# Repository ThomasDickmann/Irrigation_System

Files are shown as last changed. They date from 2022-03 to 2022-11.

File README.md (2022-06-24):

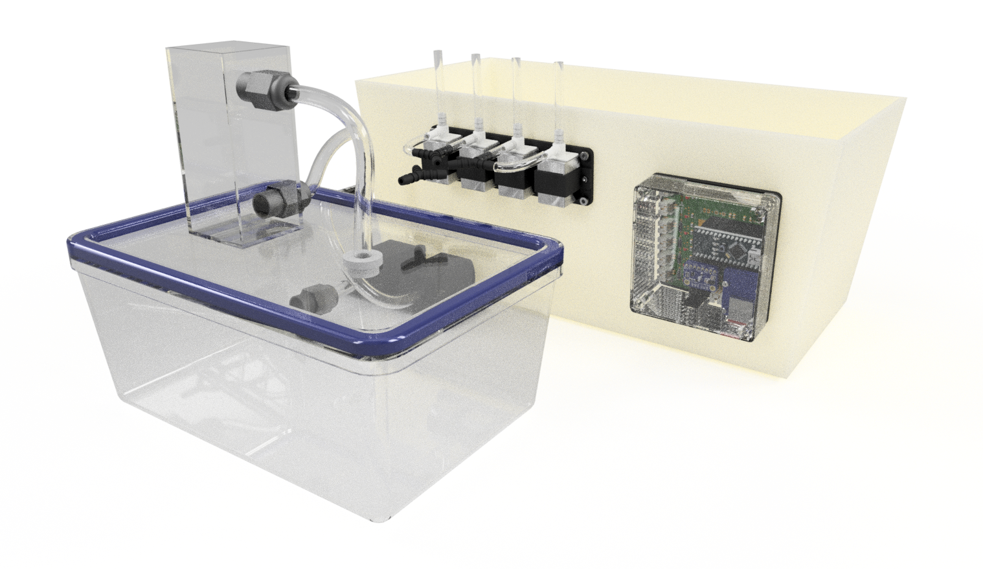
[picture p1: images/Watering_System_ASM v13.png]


# Arduino Irrigation System - WIP
The purpose of this project was to learn basic electronic design, PCB layout, and embedded software development using VS code and PlatformIO.
The project is a work in progress, so use any code with appropriate caution!

Written in 2022 by Thomas Dickmann. 

## System architecture and intended use 
The goal is to create a fully automated irrigation system to be used in a home automation context. The hardware is capable of controlling two 12V pumps and four 12V solenoid valves to independently give water to up to four plants. The dual pump setup is used to create a redundant safety feature to prevent flooding upon a controller malfunction. The soil moisture level is obtained using capacitive analog sensors. Additionally, a BMP280 temperature and pressure sensor can provide ambient information. Finally, the connection of a SD card module allows for data logging and a Real Time Clock (RTC) provides time stamps and allows the system to operate in an energy efficient deep sleep state in between the service routines.     

## Content 
This repo currently contains the arduino code for the controller. The project also comprises Autodesk EAGLE files for the schematic and PCB as well as a CAD package with Fusion360 and .stl files for the various mechanical parts to put together the final product. Additionally, off-the-shelf components make up a substantial part of the system, therefore a list will be published containing links to the various components that were used. 
Finally, a manual will be created after everything is wrapped up and tested. 

### Features
+ 6 MOSFET Low side switches (LSS) with indicator LEDs for valves and motors, providing 12V input power to the peripherals 
+ PWM enabled motor control for power modulation 
+ 4 analog sensor inputs with filter capacitors 
+ High Side Switch (HSS) controlling the powering of the analog sensors and SD card (powered only when in use to reduce idle energy consumption) 
+ Data logging of soil moisture levels, temperature and air pressure with time stamps for long term observation  

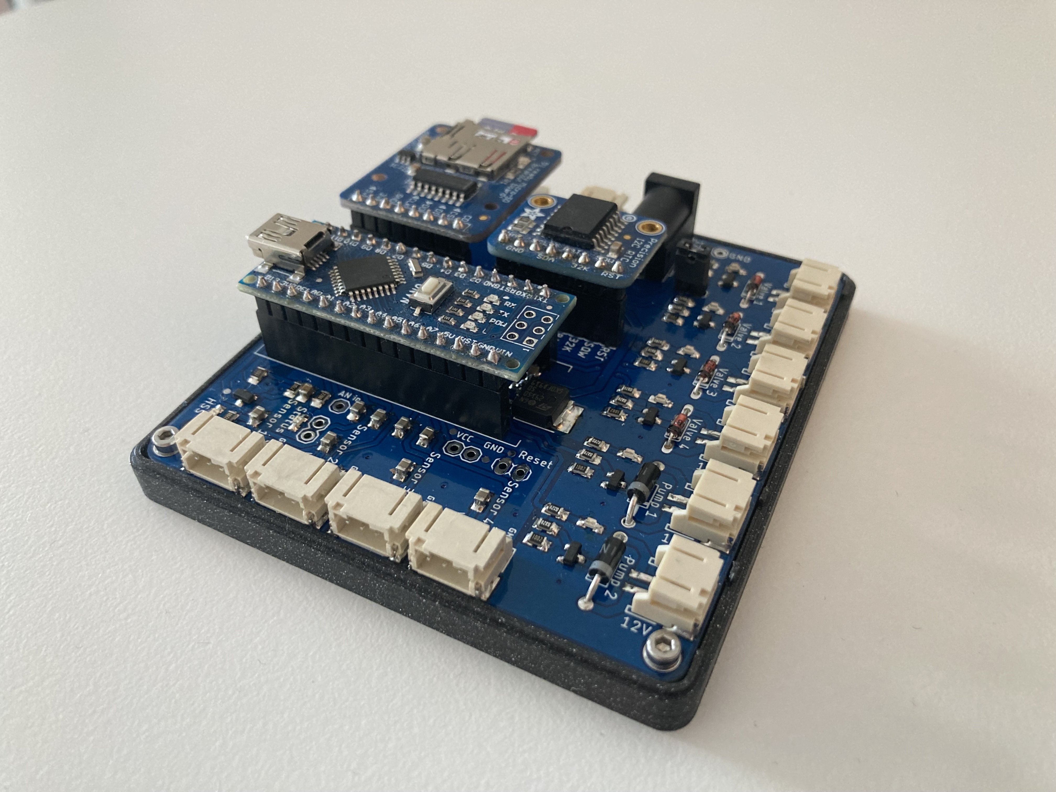
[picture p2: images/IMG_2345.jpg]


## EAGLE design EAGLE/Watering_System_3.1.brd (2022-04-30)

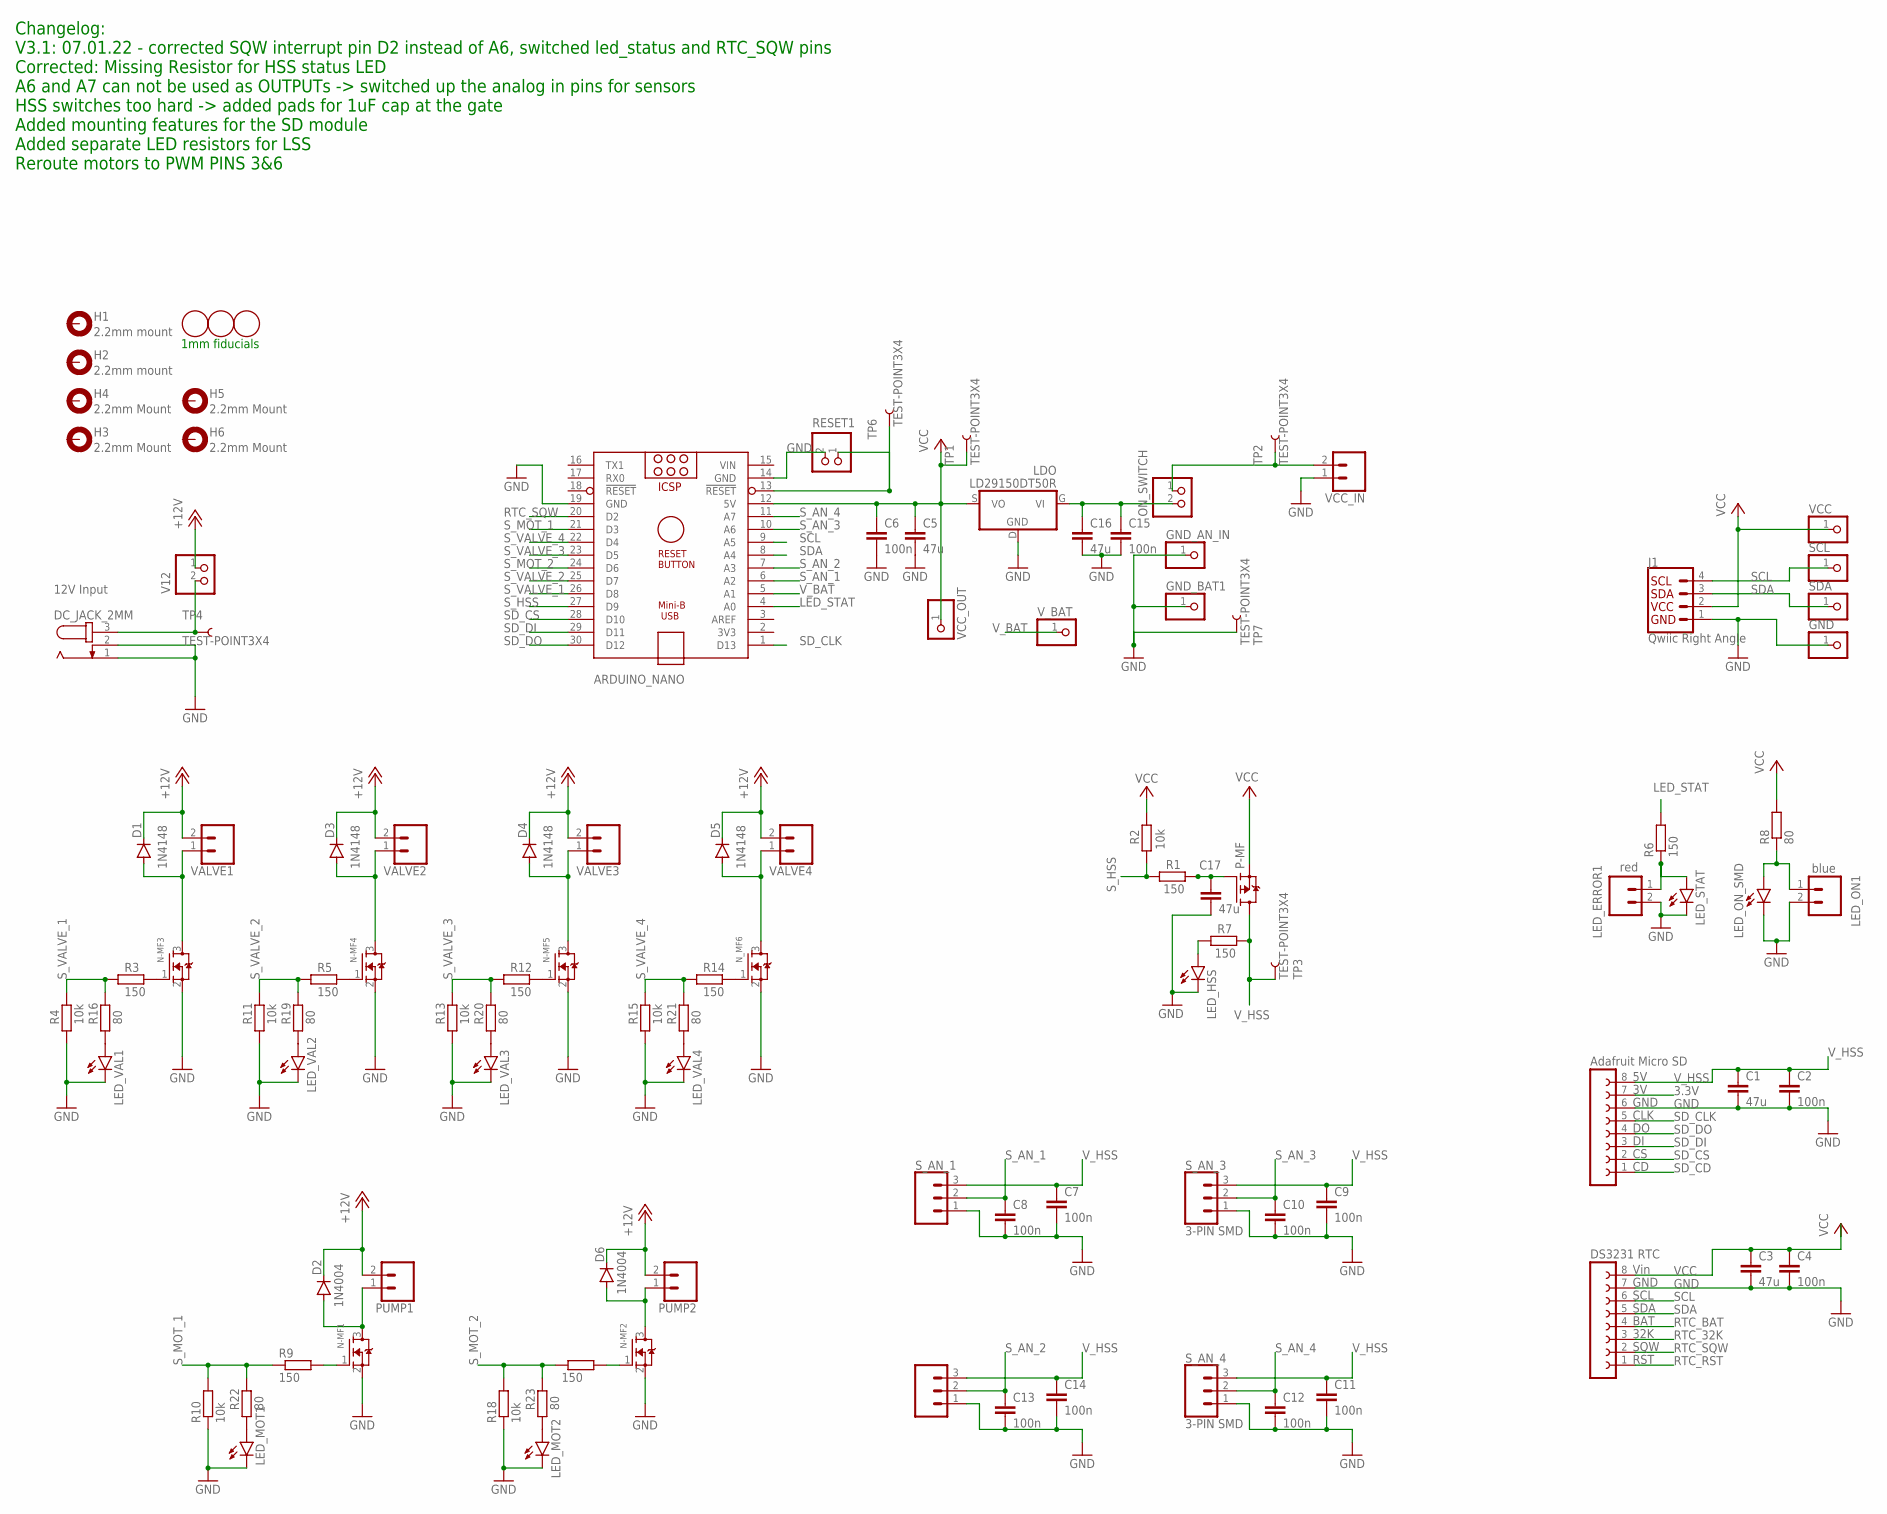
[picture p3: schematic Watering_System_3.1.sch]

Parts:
ARDUINO_NANO: ARDUINO_NANO
C1, C3, C5, C16, C17: 47u; C0805
C2, C4, C6, C7, C8, C9, C10, C11, C12, C13, C14, C15: 100n; C0805
D1, D3, D4, D5: 1N4148; DO35-7
D2, D6: 1N4004; DO41-10
DC_JACK_2MM: 12V Input; SPC4077
GND: PINHD-1X1; 1X01
GND_AN_IN: PINHD-1X1; 1X01
GND_BAT1: PINHD-1X1; 1X01
H1, H2: 2.2mm mount; 2,2-PAD
H3, H4, H5, H6: 2.2mm Mount; 2,2-PAD
J1: Qwiic Right Angle; 1X04_1MM_RA
LDO: LD29150DT50R; DPACK_2
LED_ERROR1: red; 1X02
LED_HSS: LEDCHIPLED_0805; CHIPLED_0805
LED_MOT1, LED_MOT2: LEDCHIPLED_0805; CHIPLED_0805
LED_ON1: blue; 1X02
LED_ON_SMD: LEDCHIPLED_0805; CHIPLED_0805
LED_STAT: LEDCHIPLED_0805; CHIPLED_0805
LED_VAL1, LED_VAL2, LED_VAL3, LED_VAL4: LEDCHIPLED_0805; CHIPLED_0805
N-MF1, N-MF2, N-MF3, N-MF4, N-MF5: IRLML6244TRPBF; SOT23R_INFINEON
N_MF6: IRLML6244TRPBF; SOT23R_INFINEON
ON_SWITCH: toggle_breakout; 1X02
P-MF: IRLML2244TRPBF; SOT23R_INFINEON
PUMP1, PUMP2: CONN_02-JST-2MM-SMT; JST-2-SMD
R1, R3, R5, R6, R7, R9, R12, R14, R17: 150; R0805
R2, R4, R10, R11, R13, R15, R18: 10k; R0805
R8, R16, R19, R20, R21, R22, R23: 80; R0805
RESET1: toggle_breakout; 1X02
RTC: DS3231; RTC
SCL: PINHD-1X1; 1X01
SC_CARD: MIRCO_SD_ADAFRUITSD; ADAFRUIT_SD
SDA: PINHD-1X1; 1X01
S_AN_1, S_AN_2, S_AN_3, S_AN_4: 3-PIN SMD; JST-3-SMD
TP1, TP2, TP3, TP4, TP6, TP7: TEST-POINT3X4; PAD.03X.04
U$1, U$2, U$3: FIDUCIAL; FIDUCIAL_1MM
V12: toggle_breakout; 1X02
VALVE1, VALVE2, VALVE3, VALVE4: CONN_02-JST-2MM-SMT; JST-2-SMD
VCC: PINHD-1X1; 1X01
VCC_IN: CONN_02-JST-2MM-SMT; JST-2-SMD
VCC_OUT: PINHD-1X1; 1X01
V_BAT: PINHD-1X1; 1X01

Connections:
3.3V: SC_CARD.7 (3V)
+12V: D1.C, D2.C, D3.C, D4.C, D5.C, D6.C, PUMP1.2 (1), PUMP2.2 (1), V12.1, VALVE1.2 (1), VALVE2.2 (1), VALVE3.2 (1), VALVE4.2 (1)
GND: ARDUINO_NANO.14 (GND), ARDUINO_NANO.19 (GND), C1.2, C2.2, C3.2, C4.2, C5.2, C6.2, C7.2, C8.2, C9.2, C10.2, C11.2, C12.2, C13.2, C14.2, C15.2, C16.2, C17.2, DC_JACK_2MM.1, DC_JACK_2MM.2, GND.1, GND_AN_IN.1, GND_BAT1.1, J1.1, LDO.D (GND), LED_ERROR1.2, LED_HSS.C, LED_MOT1.C, LED_MOT2.C, LED_ON1.2, LED_ON_SMD.C, LED_STAT.C, LED_VAL1.C, LED_VAL2.C, LED_VAL3.C, LED_VAL4.C, N-MF1.2 (S), N-MF2.2 (S), N-MF3.2 (S), N-MF4.2 (S), N-MF5.2 (S), N_MF6.2 (S), R4.1, R10.1, R11.1, R13.1, R15.1, R18.1, RESET1.2, RTC.7 (GND), SC_CARD.6 (GND), S_AN_1.1, S_AN_2.1, S_AN_3.1, S_AN_4.1, TP7.P$1, VCC_IN.1 (2)
LED_STAT: ARDUINO_NANO.4 (A0), R6.2
unnamed: N-MF1.1 (G), R9.2
unnamed: D3.A, N-MF4.3 (D), VALVE2.1 (2)
unnamed: LED_ON1.1, LED_ON_SMD.A, R8.1
unnamed: N-MF2.1 (G), R17.2
unnamed: LED_ERROR1.1, LED_STAT.A, R6.1
unnamed: LED_HSS.A, R7.1
unnamed: D1.A, N-MF3.3 (D), VALVE1.1 (2)
unnamed: N-MF4.1 (G), R5.2
unnamed: D4.A, N-MF5.3 (D), VALVE3.1 (2)
unnamed: C17.1, P-MF.1 (G), R1.2
unnamed: N-MF3.1 (G), R3.2
unnamed: N-MF5.1 (G), R12.2
unnamed: D5.A, N_MF6.3 (D), VALVE4.1 (2)
unnamed: N_MF6.1 (G), R14.2
unnamed: C15.1, C16.1, LDO.G (VI), ON_SWITCH.2
unnamed: DC_JACK_2MM.3, TP4.P$1, V12.2
unnamed: LED_VAL1.A, R16.1
unnamed: D2.A, N-MF1.3 (D), PUMP1.1 (2)
unnamed: D6.A, N-MF2.3 (D), PUMP2.1 (2)
unnamed: LED_VAL2.A, R19.1
unnamed: ARDUINO_NANO.13 (!RESET), RESET1.1, TP6.P$1
unnamed: ON_SWITCH.1, TP2.P$1, VCC_IN.2 (1)
unnamed: LED_VAL3.A, R20.1
unnamed: LED_VAL4.A, R21.1
unnamed: LED_MOT1.A, R22.1
unnamed: LED_MOT2.A, R23.1
RTC_32K: RTC.3 (32K)
RTC_BAT: RTC.4 (BAT)
RTC_RST: RTC.1 (RST)
RTC_SQW: ARDUINO_NANO.20 (D2), RTC.2 (SQW)
SCL: ARDUINO_NANO.9 (A5), J1.4, RTC.6 (SCL), SCL.1
SDA: ARDUINO_NANO.8 (A4), J1.3, RTC.5 (SDA), SDA.1
SD_CD: SC_CARD.1 (CD)
SD_CLK: ARDUINO_NANO.1 (D13), SC_CARD.5 (CLK)
SD_CS: ARDUINO_NANO.28 (D10), SC_CARD.2 (CS)
SD_DI: ARDUINO_NANO.29 (D11), SC_CARD.3 (DI)
SD_DO: ARDUINO_NANO.30 (D12), SC_CARD.4 (DO)
S_AN_1: ARDUINO_NANO.6 (A2), C8.1, S_AN_1.2
S_AN_2: ARDUINO_NANO.7 (A3), C13.1, S_AN_2.2
S_AN_3: ARDUINO_NANO.10 (A6), C10.1, S_AN_3.2
S_AN_4: ARDUINO_NANO.11 (A7), C12.1, S_AN_4.2
S_HSS: ARDUINO_NANO.27 (D9), R1.1, R2.1
S_MOT_1: ARDUINO_NANO.21 (D3), R9.1, R10.2, R22.2
S_MOT_2: ARDUINO_NANO.24 (D6), R17.1, R18.2, R23.2
S_VALVE_1: ARDUINO_NANO.26 (D8), R3.1, R4.2, R16.2
S_VALVE_2: ARDUINO_NANO.25 (D7), R5.1, R11.2, R19.2
S_VALVE_3: ARDUINO_NANO.23 (D5), R12.1, R13.2, R20.2
S_VALVE_4: ARDUINO_NANO.22 (D4), R14.1, R15.2, R21.2
VCC: ARDUINO_NANO.12 (5V), C3.1, C4.1, C5.1, C6.1, J1.2, LDO.S (VO), P-MF.2 (S), R2.2, R8.2, RTC.8 (VIN), TP1.P$1, VCC.1, VCC_OUT.1
VIN: ARDUINO_NANO.15 (VIN)
V_BAT: ARDUINO_NANO.5 (A1), V_BAT.1
V_HSS: C1.1, C2.1, C7.1, C9.1, C11.1, C14.1, P-MF.3 (D), R7.2, SC_CARD.8 (5V), S_AN_1.3, S_AN_2.3, S_AN_3.3, S_AN_4.3, TP3.P$1

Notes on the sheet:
1mm fiducials
Changelog: V3.1: 07.01.22 - corrected SQW interrupt pin D2 instead of A6, switched led_status and RTC_SQW pins Corrected: Missing Resistor for HSS status LED A6 and A7 can not be used as OUTPUTs -> switched up the analog in pins for sensors HSS switches too hard -> added pads for 1uF cap at the gat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

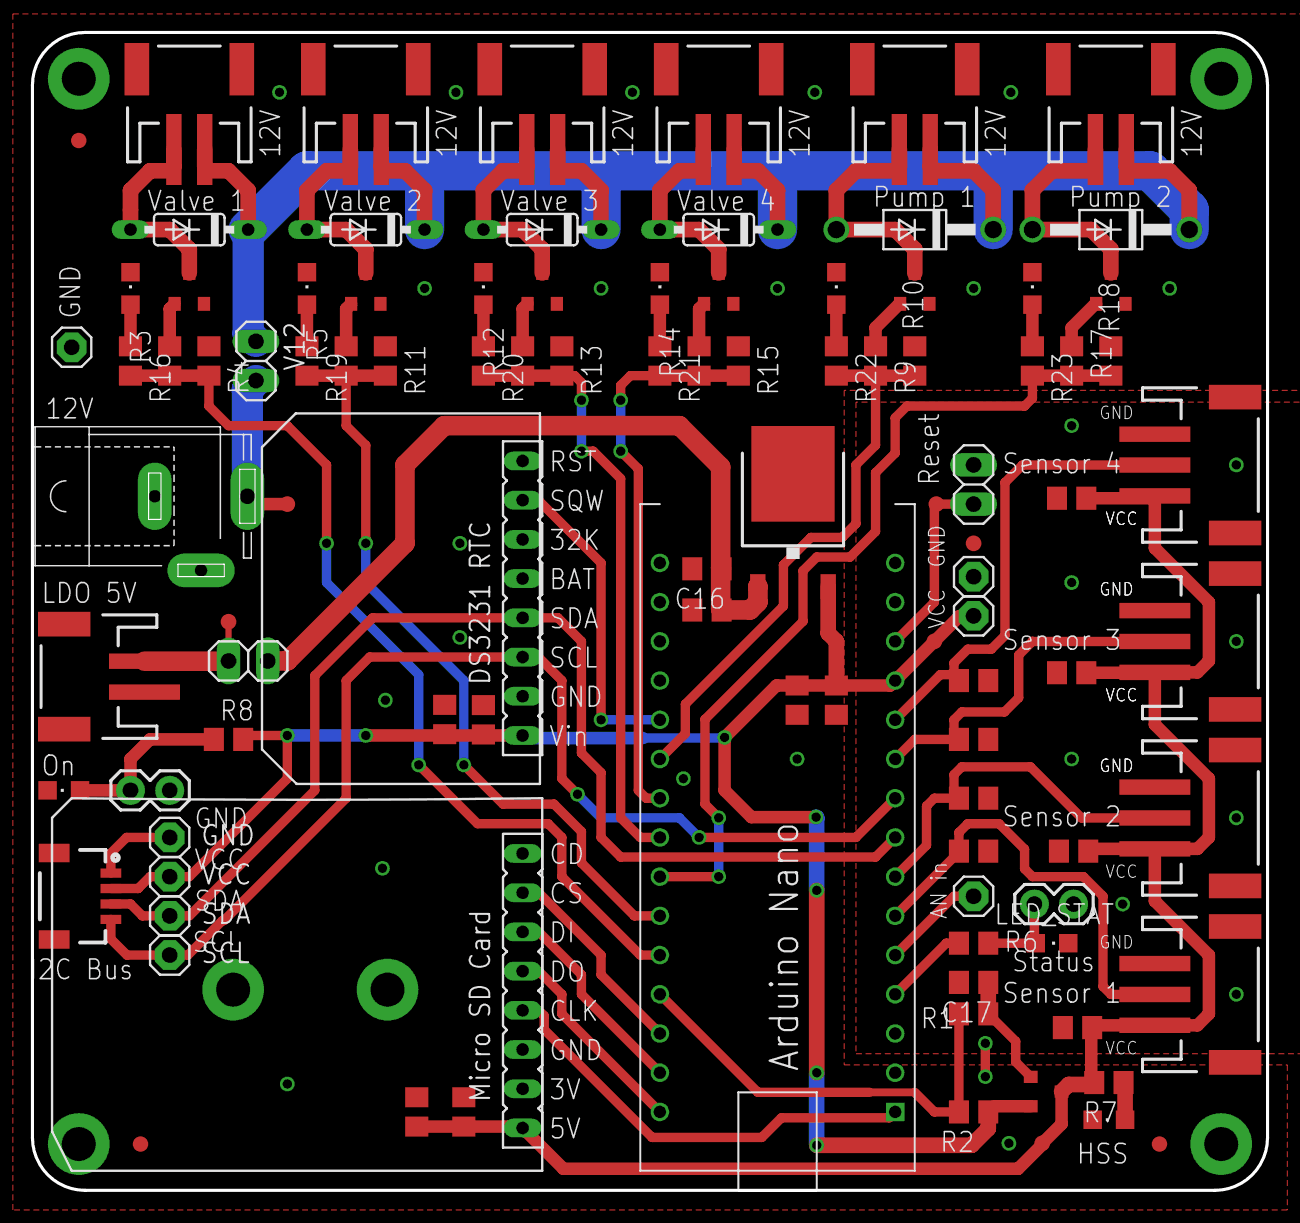
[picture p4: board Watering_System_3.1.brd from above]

Board: 2 copper layers, 80.0 x 75.0 mm, 107 parts (0 on the bottom side), 50 nets.

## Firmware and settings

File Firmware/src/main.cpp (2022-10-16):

/***************************************
 *      Arduino Irrigation System V3.1
 *      Written by Thomas Dickmann
 *      Started 09.01.2022
 ***************************************/

//Using Platformio requires to include the Arduino framework 
#include <Arduino.h>

/**********************************************************************************************************
 *  OPL project: 
 * 
 * TODO: Resolve conflict with RTC and BMP. When taking RTC out of the picture completely, things seem to work fine 
 * No address conflict - checked via I2C scanner:
 * RTC I2C address is 0x68 
 * BMP I2C address is 0x76
 * TODO: Sleep.h not found when using 33IoT envorionment in Platformio.ini (build): https://www.arduino.cc/reference/en/libraries/arduino-low-power/
 * TODO: When putting multiple environments in the platformio.ini file, the serial monitor doesn't work anymore 
 * TODO: Flesh out pseudo code for service routine 
 * TODO: aggressive behavior invoked error with loop over object array
 * TODO: Add array of water amounts per plant
 * TODO: warning comparison of signed and unsigned int with sizeof function in for loop 
 * TODO: correct value of ml_per_sec constant in setup.cpp
 * TODO: Include BMP280 functionality 
 * TODO: Set correct RTC time 
 * TODO: Move SD functionality to setup.cpp 
 * TODO: Use list of objects to cycle over for initialization? Less repeatative code
 * TODO: Open and write sensor Data on SD card every service cycle 
 * TODO: Clean up and understand RTC setup and ISR/interrupt handling 
 * TODO: Move time offset out of set alarm function, make input for function (clearer concept)
 * TODO: Fix overflow problem with Seconds >60 values for interrupt alarm timer -> extrpolate to hours
 * TODO: Better understand SD functions 
 * TODO: BP writing multiple variables in constant format string -> Input Master Thesis %D%D%D%D%D w/ const digit space 
 * TODO: How to use the LED object and LED.cpp functions in SD setup function? 
 * 
 * TODO: Reserach target specific code sections (IoT33 vs. regular nano): https://community.platformio.org/t/changing-destination-boards/4751/2
 * 
 * Done 09.01.: Mixup with analog pins. Schematic adjusted and prototype resoldered, need to be fixed in PCB V3.1 (reorder) 
 * Done 12.01.: Understand where to declare which variables without conflict and follow BP -> Use of extern and move of declarations into setup.cpp
 * Done 12.01.: When creating Setup.cpp file, the build fails. Error: Multiple definitions of the pin variables.--> Declaration instead of definition in header file (see above) 
 * Done 12.01.: Refactor code and move init functions to setup.cpp 
 * Done 12.01.: Set up basic SD functionality in loop 
 * Done 12.01.: Added pseudocode for service routine 
 * Done 16.01.: Added blinking LED in SD setup function (indicating setup failure)
 * Done 16.01.: Created object arrays for valves and sensors 
 * Done 16.01.: Created watering routines using for loop over object arrays (DRY-logic)
 * ********************************************************************************************************/

//Setup and Hardware classes includes 
#include "Setup.h" //including system constants and RTC + SD related routines
#include "LED.h" //class for LEDS
#include "LowSideSwitch.h" //class for LSS drivers
#include "HighSideSwitch.h" //class for HSS stages
#include "AnalogInput.h" //analog sensor class 

//Creating hardware objects 
LED LED_Status(ledpin); 

LowSideSwitch Valve1(valve_1); 
LowSideSwitch Valve2(valve_2); 
LowSideSwitch Valve3(valve_3); 
LowSideSwitch Valve4(valve_4); 

LowSideSwitch Motor1(mot_1); 
LowSideSwitch Motor2(mot_2);

HighSideSwitch HSS(hss_sig); 
 
AnalogInput Sensor1(sen_1); 
AnalogInput Sensor2(sen_2); 
AnalogInput Sensor3(sen_3); 
AnalogInput Sensor4(sen_4); 

//Creating a list of objects to loop over in the service cylce 
AnalogInput MySensors[] = {Sensor1, Sensor2, Sensor3, Sensor4};
LowSideSwitch MyValves[] = {Valve1, Valve2, Valve3, Valve4};

//Creation of File object for SD card 
//TODO: Move to setup.cpp? Possible/correct practise? 
File myData; 

//Creation of BMP sensor object
Adafruit_BMP280 bmp; 
//CHECK - object creation doesn't fuck up the serial communication 

void setup()
{
  //Initializing the hardware objects (pins, default states) 
  //Motors off, valves closed, HSS power on
  LED_Status.init(); 

  Valve1.init(); 
  Valve2.init();
  Valve3.init(); 
  Valve4.init(); 

  Motor1.init();
  Motor2.init();

  HSS.init(); 

  Sensor1.init(); 
  Sensor2.init(); 
  Sensor3.init(); 
  Sensor4.init(); 

  //Starting serial communication
  Serial.begin(115200); 
  
/********************************************   
*   Initial test of hardware and peripherals
*********************************************/

  //  *** Valves and motors check *** 
  //Open the valves sequentially 
  Serial.println("Checking valves and motors... "); 
  for (int i=0; i <4; i++){
    MyValves[i].on();
    delay(150);
  }
  //start both motors, fill up reservoir and lines 
  Motor1.on();
  delay(2000); //reservoir buffer needs to be bigger to prevent dry run on pump 2
  Motor2.on();
  delay(500); //TODO: Adjust, so that lines will be filled but little to no water makes it through the valves
  //stop pumps
  Motor1.off(); 
  Motor2.off(); 
  //close valves 
  for (int i=0; i <4; i++){
    MyValves[i].off();
  }
  Serial.println("Valve and motor check finished. \n"); 

   //  *** Sensors and SD card check *** 
  //Powering the HSS 
  HSS.on(); 

//Adding the sensor check leads to SD card not being able to open the file... wtf. 
/* 
  //Checking the analog sensor readings: 
  Serial.println("Checking soil sensors and water demand... "); 
  for (int i=0; i <4; i++){
  Serial.print("Sensor "); 
  Serial.print(i+1);
  Serial.print(": ");
  Serial.println(MySensors[i].read());
  if(MySensors[i].read()  <  soil_threshold){
      Serial.print("Watering need detected. Watering plant ");
      Serial.println(i+1); 
    }
  else{ 
      Serial.print("No watering need detected for plant ");
      Serial.println(i+1); 
    }
  }
Serial.println("Analog sensor check finished. \n"); 
*/

 
  //When using the BMP, the code compiles, but it fucks up the RTC timestamps on the serial monitor 
  bmp.begin(BMP280_ADDRESS_ALT, BMP280_CHIPID); //adressing BMP with correct bus adress 
  //CHECK - Object initialization fucks up writing the timestamp data entry for the SD card to the monitor
    bmp.setSampling(Adafruit_BMP280::MODE_NORMAL,     // Operating Mode. 
          Adafruit_BMP280::SAMPLING_X2,               // Temp. oversampling 
          Adafruit_BMP280::SAMPLING_X16,              // Pressure oversampling 
          Adafruit_BMP280::FILTER_X16,                // Filtering. 
          Adafruit_BMP280::STANDBY_MS_500);           // Standby time. 
  //CHECK - Settings don't seem to fuck up more stuff 

  //  *** RTC setup and check *** 
/*
  //Initializing RTC (only needed once)
  RTC_setup(); 
*/ 

 //flashing the status LED to indicate to signal finish of setup function 
  for (int i=0; i <4; i++){
    LED_Status.on();
    delay(150);
    LED_Status.off(); 
    delay(150);
  }

  Serial.println("System check and setup cycle finished. \n"); 
  //End of setup function 
}


void loop()
{
/*************************************************
* Code for the sleep state routine between loops *
**************************************************/

Serial.println("--- Set alarm and initialize SD card --- ");  
  /*
  //Set new alarm with defined time offset 
  RTC_set_alarm(); //Writes the new alarm time to the serial monitor
  delay(100); 
  //Hypothesis: Serial was doing weird shit because the final step in set_alarm is to write the time, while the first step in the next function was to get the time.
  //probably timestap changed while trying to write it to the serial when calling set_alarm right right after calling it before in setup, or after sleep prepare with get timestamp

  //Preparing the arduino for power saving sleep state ... TODO: Move sleep_cpu to RTC_sleep_prepare fct?
  RTC_sleep_prepare(); //writes the time of going to sleep to the serial monitor 
  delay(100); 
  sleep_cpu();  //activating sleep mode
*/

  //Code to be executed after arduino has been woken up:
  LED_Status.on(); //turns on status led to indicate wakeup/begin of service cycle
  HSS.on();        //connecting power to sensors and SD card 

/*                                        
  //Get current time stamp from RTC
  get_timestamp(); 
  //Printing wakeup time to the serial monitor
  Serial.println("Controller has been woken up");
  Serial.print("Time: ");
  Serial.print(String(hour(t)));
  Serial.print(":");
  Serial.print(String(minute(t)));
  Serial.print(":");
  Serial.println(String(second(t)));  
*/
  //Initializing the SD after powering it down (error indication by status led, won't work on PCB V3.0)
  SD_setup(ledpin); 

  //Allowing the system to settle for a while
  delay(300); 

  Serial.println("--- Service cycle begin --- \n"); 

  /****************************************
  *** Code for reading all sensor data ****
  *****************************************/

  //BMP 280 temperature and pressure sensor 
  Serial.print(F("Temperature = "));
  Serial.print(bmp.readTemperature());
  Serial.println(" *C");
  Serial.print(F("Pressure = "));
  Serial.print(bmp.readPressure());
  Serial.println(" hPa");
  //CHECK - Using these functions in Loop fucks up the RTC and Serial real good. No more Strings before timestamps in set_alarm and sleep_prepare, timestamp SD only consists of seconds


  //Create logging entry for SD card 
  Serial.println("Creating data entry for SD card:");
  //timestamp = (String(year(t)) +"/" +String(month(t)) +"/" +String(day(t)) +" - " +String(hour(t))+":"+String(minute(t))+":"+String(second(t)));  
  //String sensor_data = (String sensor 1-4, string temperature, string pressure, string amount)
  Serial.println("testprint"); //+ sensor_data
  //TODO: create string object in setup and only overwrite the value here each time the service cycle is performed
  //TODO: Write newly overwritten string object to sd card with function (input string, function details in setup.cpp)

  //Test code for SD card functionality 
  myData = SD.open("data.txt", FILE_WRITE);
  if (myData) {
    Serial.print("Writing to file... ");
    // Write to file
    myData.print(String(hour(t)));
    myData.print(":");
    myData.print(String(minute(t)));
    myData.print(":");
    myData.println(String(second(t))); 
   
    myData.print("Data Sensor 1"); 
    myData.print("Data Sensor 2"); 
    myData.print("Data Sensor 3"); 
    myData.print("Data Sensor 4");

    myData.print("Bool Pump 1");
    myData.print("Bool Pump 2");

    myData.close(); // close the file

    Serial.println("Data written successfully! \n");
  }
  // if the file didn't open, print an error:
  else {
    Serial.println("Error opening data.txt \n");
  }



/****************************************
** Code for watering service routine ****
*****************************************/

 //Fill secondary reservoir with water
 Motor1.on(); 
 delay(2000); //TODO pass fuction to give 15ml of water 
 Motor1.off();
 
 //Loop over sensors and compare values to threshold (needs to be defined in setup.cpp) 
  Serial.println("Reading soil sensors, checking for water demand: "); 
  for (int i=0; i <4; i++){
  Serial.print("Sensor "); 
  Serial.print(i+1);
  Serial.print(": ");
  Serial.println(MySensors[i].read());

  if(MySensors[i].read()  <  soil_threshold){
      Serial.print("Watering need detected. Watering plant ");
      Serial.println(i+1); 
      MyValves[i].on(); //open valve i
      Motor2.on(); //switch on pump secondary reservoir
      delay(1000); //TODO pass function to give 5ml of water, optimize with plant specific value through var. list of amount constants 
      Motor2.off(); //turn off pump secondary reservoir 
      MyValves[i].off(); //close valve i
    }

  else{ 
      Serial.print("No watering need detected for plant ");
      Serial.println(i+1); 
    }
  }


  //TODO: Create entry for amount in data entry for routine 

  //Redundant security measure: Close all valves and swtich off both pumps again
  Motor1.off(); 
  Motor2.off(); 
  Valve1.off();
  Valve2.off();
  Valve3.off(); 
  Valve4.off();  

  LED_Status.off(); //turns off status led to indicate finished service cycle
  HSS.off();        //disconnecting power to sensors and SD card 

  Serial.println("--- Service cycle finished! ---\n");

  //End of loop function 
  
  } 

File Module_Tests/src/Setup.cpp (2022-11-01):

#include "Setup.h"

/*********************************************
* Definition of constants for the system  
**********************************************/

//*** Hardware constants (see Setup.h for declaration) ***

//RTC Pins 
const unsigned char interruptPin = 2; //SQW pin connected to interrupt0 on pin D2 on Nano 
//A4 SDA
//A5 SCL 
//RST not connected
//BAT not connected 

//SD card pins 
const unsigned char CS = 10; //chip select pin 
//D11 MOSI 
//D12 MISO 
//D13 CLK

//Pinout for the PCB/Prototype circuit: 
//Indicator/status LED pin
unsigned char ledpin = A0;

//MOSFET driver pins low side switches
unsigned char valve_1 = 8; 
unsigned char valve_2 = 7; 
unsigned char valve_3 = 5; 
unsigned char valve_4 = 4;
 
unsigned char mot_1 = 3;  
unsigned char mot_2 = 6; 

//MOSFET driver pin high side switch 
unsigned char hss_sig = 9; 

//input pins soil sensors
unsigned char sen_1 = A2;
unsigned char sen_2 = A3; 
unsigned char sen_3 = A6; 
unsigned char sen_4 = A7; 

//input pin battery voltage
unsigned char v_bat = A1; 

//*** Firmware constants/variables (not included in Setup.h) ***

//Time interval for system wake-up cycles 
int wakeup_interval = 5; //TODO: Check, if int necessary

//Variables of the system 
time_t t; //Time variable to be used in RTC functions 

// Creation of sensor reading variables soil sensors 
unsigned short value1; 
unsigned short value2; 
unsigned short value3; 
unsigned short value4; 

unsigned short soil_threshold = 1000; 

// Creation of sensor reading variables BMP
float temperature_current;
float pressure_current;


/*********************************************
* Function bodies for the system setup 
**********************************************/

//Real time clock functionality

//Function triggered when interrupt has fired (used in function "attachInterrupt") 
//Wakes up the arduino from sleep state and detatches the interrupt
void wakeUp()
{
  Serial.println(F("Alarm interrupt has been triggered, controller is waking up..."));   //Print message to serial monitor
  sleep_disable();                                         //Disable sleep mode
  detachInterrupt(digitalPinToInterrupt(interruptPin));    //Removes the interrupt from pin 2;
}


//Function to initialize the RTC, clear the alarm etc (unmodified copy from tutorial)
// initialize the alarms to known values, clear the alarm flags, clear the alarm interrupt flags
void RTC_alarm_init()
{
    pinMode(interruptPin, INPUT_PULLUP);
    //unmodified from tutorial: 
    RTC.setAlarm(ALM1_MATCH_DATE, 0, 0, 0, 1);
    RTC.setAlarm(ALM2_MATCH_DATE, 0, 0, 0, 1);
    RTC.alarm(ALARM_1);
    RTC.alarm(ALARM_2);
    RTC.alarmInterrupt(ALARM_1, false);
    RTC.alarmInterrupt(ALARM_2, false);
    RTC.squareWave(SQWAVE_NONE);
    Serial.println(F("RTC initialization complete"));
}

//Set an Alarm 
void RTC_set_alarm()
{
  t=RTC.get();//Gets the current time of the RTC
  //TODO: include if statement here to check the potential overflow after adding wakeup_interval, then proceed 
  // ... if second(t) > 60-wakeup_interval{
  //  
  //  }
  RTC.setAlarm(ALM1_MATCH_SECONDS , second(t) + wakeup_interval, 0, 0, 0);      // Setting alarm 1 to go off every wakeup_interval seconds 
    // RTC.setAlarm(ALM1_MATCH_HOURS , 0, 0, hour(t) + wakeup_interval, 0);     // Later: Setting alarm 1 to go off once per hour for ramp up phase
    // clear the alarm flag
  RTC.alarm(ALARM_1);
    // configure the INT/SQW pin for "interrupt" operation (disable square wave output)
  RTC.squareWave(SQWAVE_NONE);
    // enable interrupt output for Alarm 1
  RTC.alarmInterrupt(ALARM_1, true);
  Serial.println(F("Alarm has been set for: TODO ")); 
  //TODO: Add print of alarm flag time 
}

//preparing the arduino to go to sleep:
void RTC_sleep_prepare()
  {
  sleep_enable(); 
  attachInterrupt(digitalPinToInterrupt(interruptPin), wakeUp, LOW);    //attaching the interrupt, function "wakeUp" is executed when triggered---> here: Function/ISR definition!
  set_sleep_mode(SLEEP_MODE_PWR_DOWN);                                  //setting the deepest sleep mode                                                          //creates temporary variable with information on time
  t=RTC.get();                                                          //gets current time from RTC
  Serial.println(F("Going to sleep... (TODO: Sleep time)")); 
 // TODO: print sleep time on serial monitor
  }


//SD data logging functionality

void SD_init(unsigned char ledpin)
   {
    Serial.print(F("Initializing SD card..."));

    if (!SD.begin(CS))
       {
           Serial.println(F("initialization failed!"));
           while (true) // endless while loop with blinking indicator led showing the error
           {
               digitalWrite(ledpin, HIGH);
               delay(200);
               digitalWrite(ledpin, LOW);
               delay(200);
           }
       }
    Serial.println(F("initialization done."));
   }


  //Service cycle functions 

  int duration_for_ml(char amount_ml)
    {
      int duration = 1000;  //amount_ml * ml_per_sec*10000 in [ms] 
      return duration; 
    }



// Function declarations

// Initialize SD card

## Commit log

2022-01-02 Project framework created
2022-03-13 fix unsigned signed comparison error sensor data
    [main.cpp]
2022-04-30 pcb images added
2022-04-30 add PCB layout data
    [Watering_System_3.1.brd, Watering_System_3.1.sch]
2022-06-24 add valve/motor check routine in setup
2022-06-24 add and comment analog sensor check - sd issues
    [main.cpp]
2022-10-16 add Serial.print(F(...)) everywhere -> saves RAM!
2022-10-23 fix sensor numbering bug, only '*' possible for String temp
    [main.cpp]
2022-11-01 baseline commit - system before alarm interrupts
2022-11-01 add alarm interrupt routine, system works as intended

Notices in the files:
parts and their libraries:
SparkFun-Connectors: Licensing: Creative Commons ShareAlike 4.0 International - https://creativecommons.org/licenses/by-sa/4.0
